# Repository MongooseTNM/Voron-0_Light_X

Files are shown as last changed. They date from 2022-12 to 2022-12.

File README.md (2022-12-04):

# Voron Zero Light X

The release of my custom X axis beam for the Voron 0/0.1 printer.

This mod was designed to provide an easy way to have a lighter X carriage at a low price. It achieves that buy using cheap aluminum bar instead of pocketed aluminum tube. Total cost of this mod is in the range of $5 while buying a pocketed tube on aliexpress costs upwards of $20.

Image of Voron Zero Light X
Image of Voron Zero Light X

## Parts Needed
- Part - Quantity - Link/Info
- XY_Joint_Right_Upper - 1 - https://github.com/MongooseTNM/Voron-0_Light_X/tree/PlateX/STLs
- XY_Joint_Left_Upper - 1 - https://github.com/MongooseTNM/Voron-0_Light_X/tree/PlateX/STLs
- Plate_X_Beam_Spacer_x2 - 2 - https://github.com/MongooseTNM/Voron-0_Light_X/tree/PlateX/STLs
- Y Endstop Adapter - 1 - https://github.com/MongooseTNM/Voron-0_Light_X/tree/PlateX/STLs
- Updated Centered Rail Installation Guide - 1 - https://github.com/MongooseTNM/Voron-0_Light_X/tree/PlateX/STLs
- Voron Spec M3 Threaded Insert - 6 - Short M3x5x4
- M3x20mm BHCS - 1 - To replace the endstop bumber mounting bolt
- M3x16mm BHCS - 3 - To replace the M3x12mm bolts that mount the original extrusion to the 3d printed parts
- The Plate Itself - 1 - .5" wide x .125" thick x 7.874" long (12.7mm wide x 3.175mm thick x 200mm long) Drilled according to the PDF

### I have included a STEP File of the whole assembly.

## Instructions

### 1. Tap Plate and Ensure Tolerances

Tap the middle 10 linear rail holes for M2

tapholes

and make sure that you can slide a M3 bolt through the outer 4 holes (2 on either side), if not, drill out with 3mm drill bit. It should be a light interference fit to reduce play between the spacer and the plate.

tolerances1

### 2. Heat Set Inserts

Insert the heat set inserts on both 3d printed spacers as shown in the photos. **Note the curved corners on one side when installing the inserts.**

heatsetinsert1
heatsetinsert2

### 3. Install X Beam

Press together the 3d printed spacer and the beam on both sides. Make sure that the holes line up and the end is as close to flush as possible.

presstogether1
lineup1

**REPLACES PAGE 71:**
Mount linear rail using M2 bolts. Use the modified rail installation guide

mountrail

**REPLACES PAGE 72:**
Then insert beam like the default instructions BUT, use M3x16 bolts instead of M3x12.

insertbeam

**REPLACES PAGE 76:**
Then bolt Endstop mount like the default instructions BUT, use a M3x20 bolt instead of M3x16.

Endstopbolt1

### 4. Endstop Adapter

Because the bottom edge of the X beam doesnt exist anymore you need to print this new Adapter and mount it so it lines up with the endstop (use glue or similar).

Endstopadapter

For me the hole on the adapter lines up with the second from the right hole on the beam.

Endstopadapter2

## You are now done with this mod! Continue with the default Voron 0 assembly guide.

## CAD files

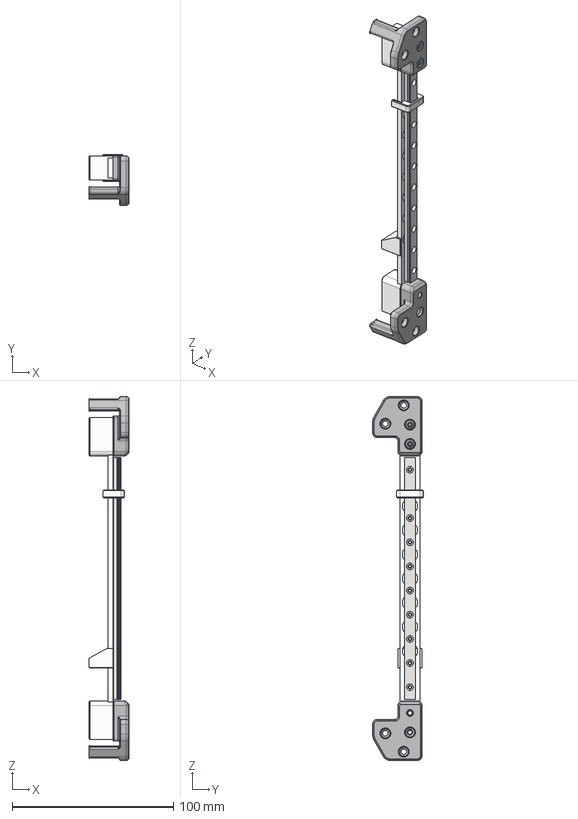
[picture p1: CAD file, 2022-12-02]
CAD/Plate Voron X Beam Assembly.step
24.8 x 31.6 x 226.0 mm
VORON_V0.1_MGN7-1
Plate X Beam Spacer x 2
M3 Insert 5D x 6L x 6
VORON_V0.1_XY_Joint_Left_Upper_x1
VORON_V0.1_XY_Joint_Right_Upper_x1
VORON_V0.1_M3x16 BHCS x 2
Centered Rail Installation Guide
Y Endstop Adapter

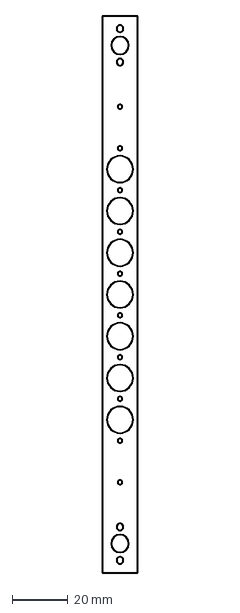
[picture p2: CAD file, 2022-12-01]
Plate Voron X Beam Drawing.dxf
12.7 x 200.0 mm

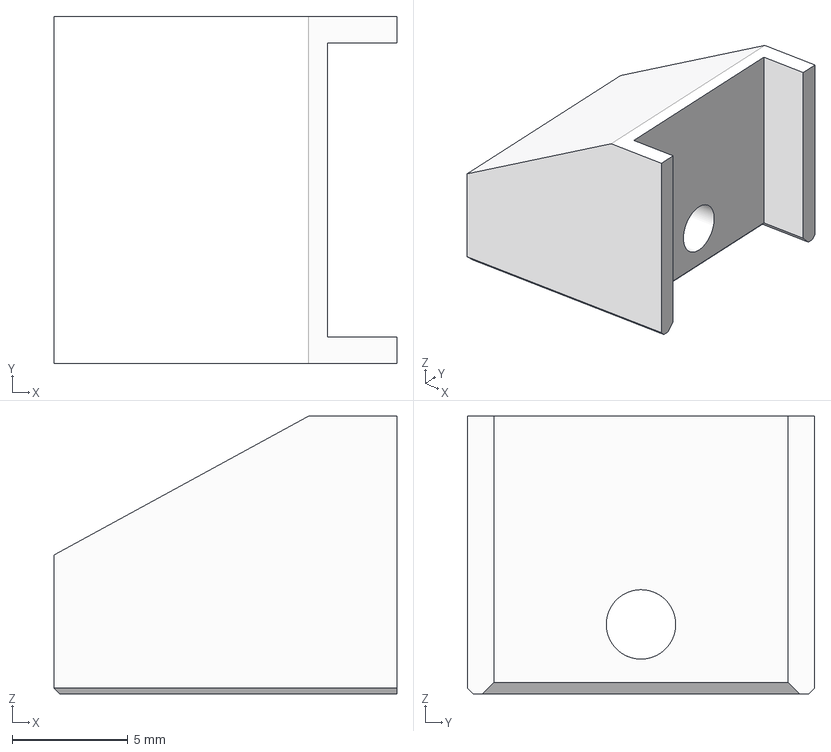
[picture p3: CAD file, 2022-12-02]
STLs/Y Endstop Adapter v4.3mf
14.8 x 15.0 x 12.0 mm

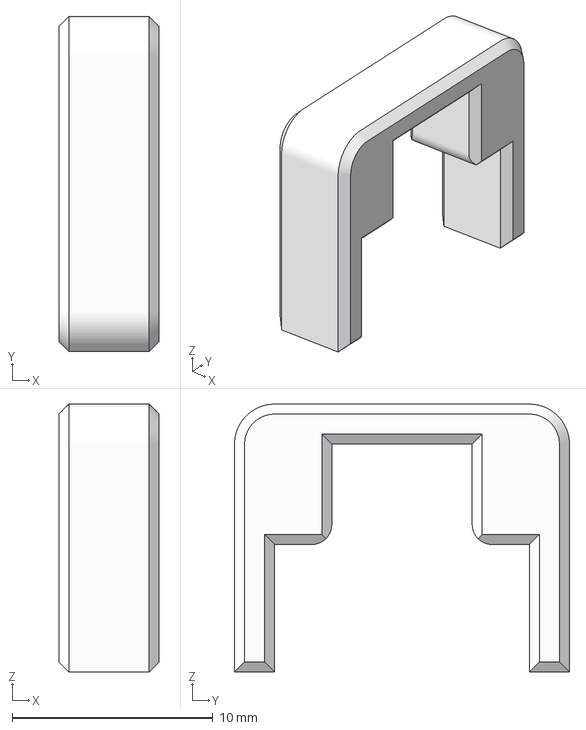
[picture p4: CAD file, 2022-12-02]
STLs/Centered Rail Installation Guide v1.3mf
5.00 x 16.7 x 13.3 mm

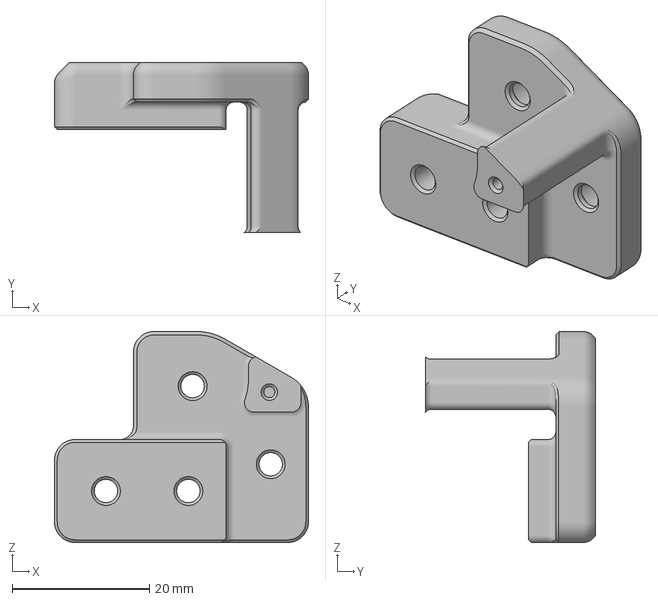
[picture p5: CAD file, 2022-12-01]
STLs/XY_Joint_Right_Upper_x1.3mf
37.0 x 24.8 x 30.7 mm

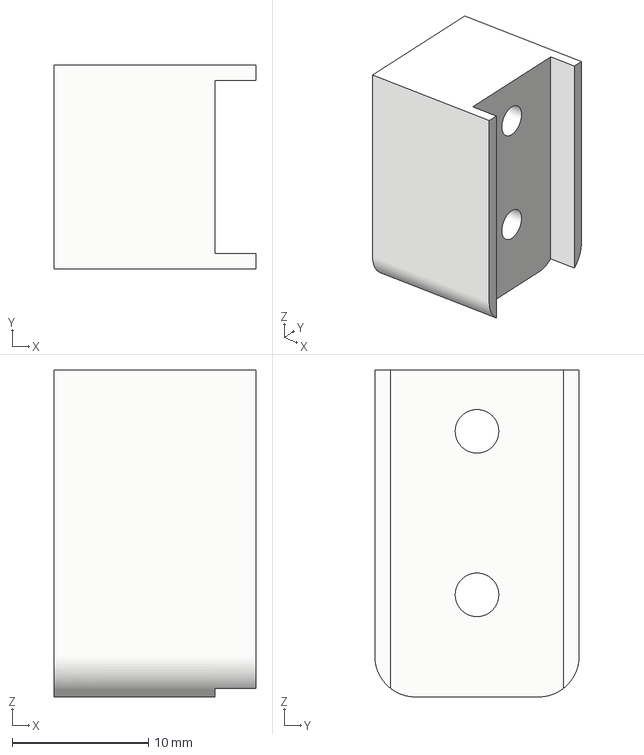
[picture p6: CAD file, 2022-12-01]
STLs/Plate_X_Beam_Spacer_x2.3mf
14.8 x 15.0 x 24.0 mm

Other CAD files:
STLs/XY_Joint_Left_Upper_x1.3mf

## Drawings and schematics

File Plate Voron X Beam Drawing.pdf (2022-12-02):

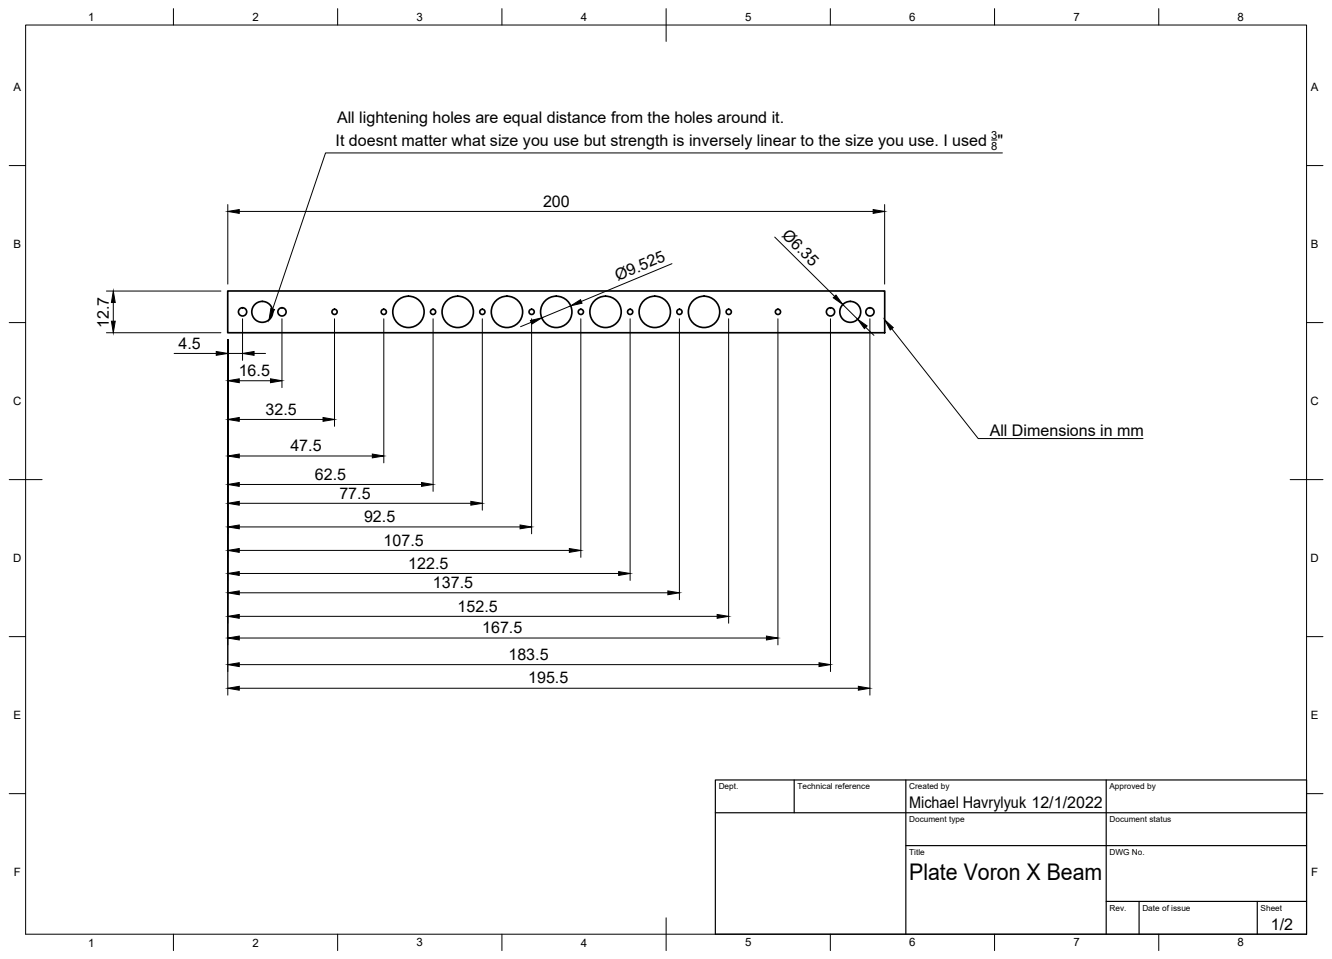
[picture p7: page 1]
Title; DWG No.; Rev.; Date of issue; Sheet

All lightening holes are equal distance from the holes around it.
It doesnt matter what size you use but strength is inversely linear to the size you use. I used 3

All Dimensions in mm

Dept. | Technical reference | Created by Michael Havrylyuk 12/1/2022 | Approved by

Document type | Document status

Plate Voron X Beam
